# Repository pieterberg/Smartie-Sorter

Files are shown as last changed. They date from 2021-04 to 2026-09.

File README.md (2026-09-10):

# Smartie Sorter 3000

   

Smartie Sorter 3000 project for sorting Smarties and M&M's based on their colour using the TCS3200 colour sensor built into a mini arcade game enclosure.

The project was written using C++ and runs on an Arduino Nano R4 microcontroller. The mini arcade game enclosure was designed using Fusion 360. The physical components were either laser-cut out of MDF and acrylic, or 3D printed using a Bambu Lab X1 Series 3D printer.

## Arduino Sketches

- The [smartie_sorter.ino](smartie_sorter/smartie_sorter.ino) sketch contains the main logic for the Smartie Sorter 3000 mini arcade game. First, the sketch initialises the Smartie Sorter 3000 after the power is switched on. The user interaction is handled by reading the button presses and providing feedback to the user through flashing the built-in LED lights. The RGB spectra of the Smarties and M&M chocolates are measured using the TCS3200 colour sensor and their colours are determined using the trained colour-detection classifier. The chocolates are then sorted using the servo motors by reading the calibrated positions stored in the EEPROM. Finally, the total number of sorted chocolates is updated and stored in the EEPROM.

- [Management.ino](management/management.ino) provides the required utilities to manage the Smartie Sorter 3000. The sketch contains code to initialise the EEPROM addresses of new Arduino boards. The management tool can then be used to generate training datasets of the RGB spectra measured by the TCS3200 colour sensor in order to train the colour-detection classifiers. An interface for calibrating the servo motors is also provided. Finally, an option is available to view the total number of sorted Smarties and M&M chocolates. These utilities can be accessed through a 9600 Baud serial channel.

## Arduino CLI

A Makefile is provided that can be used to compile and upload the Arduino sketches using the [Arduino CLI](https://github.com/arduino/arduino-cli). The make commands should all be run from the project's root directory.

First, run the install command to install the required core for the Arduino Nano R4 board. This will install the Arduino Renesas core (arduino:renesas_uno) if it is not already installed.

```shell
make install
```

The upload command can be used to compile and upload the smartie_sorter.ino sketch to the Arduino Nano R4 board. Replace the `port` parameter with the relevant port of the Arduino Nano R4 board. The ports of the attached Arduino boards can be viewed by running `arduino-cli board list` in the terminal.

```shell
make upload port=COM7
```

The upload-management command can be used to compile and upload the management.ino sketch to the Arduino Nano R4 board. Once again replace the `port` parameter with the relevant port of the Arduino Nano R4 board.

```shell
make upload-management port=COM7
```

## Git Signatures

The [signatures](./signatures) folder contains the required public SSH keys to verify the git commit signatures. These public SSH keys have been configured in the allowed_signers file.

Run the following command in the project's root directory to configure the repository's local git config file to use the allowed_signers file for verifying the git commmit signatures:

```shell
git config --local gpg.ssh.allowedSignersFile "./signatures/allowed_signers"
```

## Documentation

- [Components.md](documentation/components.md) provides information about the components used in the design of the Smartie Sorter 3000's mini arcade game enclosure. First, it provides information about the different types of components used in the design of the Smartie Sorter 3000's mini arcade game enclosure. Thereafter, it provides information about laser cutting the wooden panels and acrylic components. Finally, it provides information about the Fusion 360 computer aided design (CAD) files.

- [Design.md](documentation/design.md) provides information about the design of the Smartie Sorter 3000. First, it provides information about the name sign present at the top of the Smartie Sorter 3000's mini arcade game enclosure. Thereafter, it provides information about the Smartie Sorter 3000's colour scheme. Finally, it provides information about the sorted Smartie and M&M locations.

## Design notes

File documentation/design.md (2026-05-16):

# Design 

This document provides information about the design of the Smartie Sorter 3000. First, Section 1 provides information about the name sign present at the top of the Smartie Sorter 3000's mini arcade game enclosure. Thereafter, Section 2 provides information about the Smartie Sorter 3000's colour scheme. Finally, Section 3 provides information about the sorted Smartie and M&M locations.

The Smartie Sorter 3000 logo, colour scheme, and sorted Smartie and M&M locations were created using Affinity Designer. The `.afdesign` files are available in the [affinity_designer](https://github.com/pieterberg/Smartie-Sorter/tree/main/design/affinity_designer) folder.

### Table of Contents

- [1. Name Sign](#1-name-sign)
  - [1.1. Digital File](#11-digital-file)
  - [1.2. Enclosure Placement](#12-enclosure-placement)
- [2. Colour Scheme](#2-colour-scheme)
  - [2.1. Enclosure Design](#21-enclosure-design)
  - [2.2. Arcade Game Buttons](#22-arcade-game-buttons)
  - [2.3. Smartie Colours](#23-smartie-colours)
  - [2.4. M\&M Colours](#24-mm-colours)
- [3. Sorting Locations](#3-sorting-locations)
  - [3.1. Smartie Locations](#31-smartie-locations)
  - [3.2. M\&M Locations](#32-mm-locations)

## 1. Name Sign

This section provides information about the name sign present at the top of the Smartie Sorter 3000's mini arcade game enclosure.

The "3000" in the Smartie Sorter 3000's name comes from the TCS3200 colour sensor that the Smartie Sorter 3000 uses to determine the Smartie and M&M colours.

The logo was stylized using the Bauhaus 93 typeface.

### 1.1. Digital File

The Smartie Sorter 3000 logo is presented in Figure 1. The logo has 8 slanted stripes that correspond to the 8 Smartie colours, which are presented in Section 2.3. 

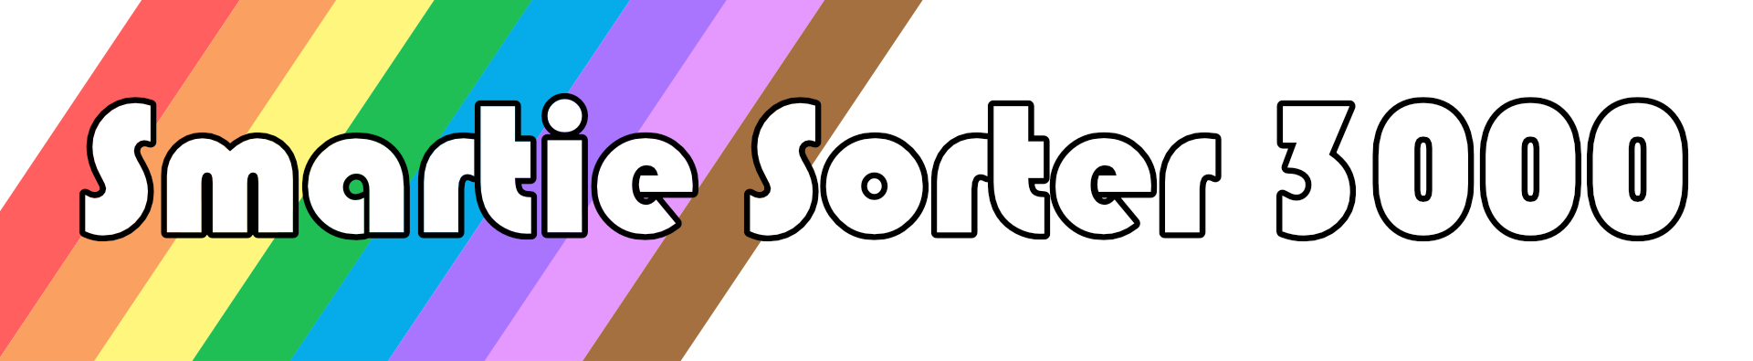
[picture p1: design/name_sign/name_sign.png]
Name sign


Figure 1: The Smartie Sorter 3000 logo used for the name at the top of the mini arcade game enclosure

The [name sign](https://github.com/pieterberg/Smartie-Sorter/tree/main/design/name_sign) folder contains both a `.png` version and an `.svg` version of the Smartie Sorter 3000 logo.

### 1.2. Enclosure Placement

The Smartie Sorter 3000 logo was printed on a 270 mm x 55 mm vinyl sticker and affixed to the Name Sign component.

The Name Sign component is backlit using 12 V LED strips present in the top-section of the mini arcade game enclosure, as documented in [electronics.md](https://github.com/pieterberg/Smartie-Sorter/blob/main/documentation/electronics.md).

## 2. Colour Scheme

This section presents the colour schemes used to design the Smartie Sorter 3000. The colour schemes and hex codes of the mini arcade game enclosure, arcade game buttons, Smartie chocolates, and M&M chocolates are provided.

The [colour_scheme](https://github.com/pieterberg/Smartie-Sorter/tree/main/design/colour_scheme) folder contains .png versions of the colour schemes.

### 2.1. Enclosure Design

The colour scheme used for the design of the mini arcade game enclosure is presented by Figure 2. The outside surfaces of the mini arcade game enclosure are painted brown while the internal surfaces of the mini arcade game enclosure are painted white.

The brown colour used for the design of the mini arcade game enclosure is based on the colour of the Rust-Oleum Painter's Touch Ultra Cover satin Nutmeg paint.

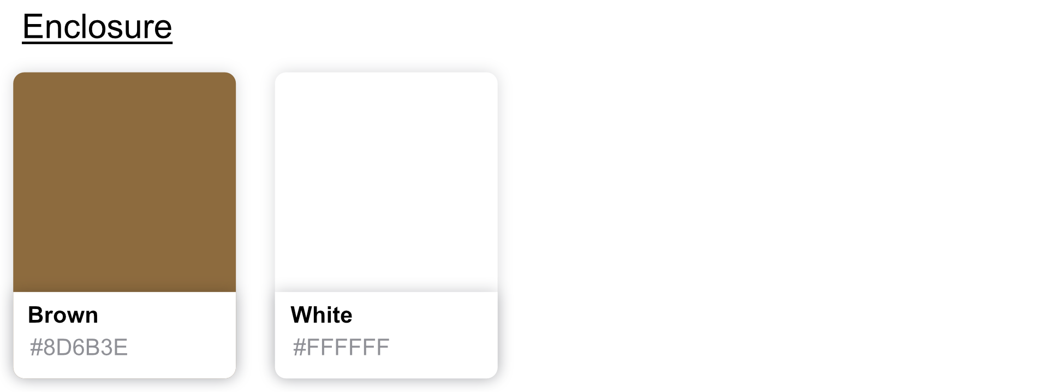
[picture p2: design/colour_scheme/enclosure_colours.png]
Enclosure colour scheme


Figure 2: The mini arcade game enclosure's colour scheme

The hex codes for the mini arcade game enclosure's colour scheme are provided in Table 1.

Table 1: The hex codes for the mini arcade game enclosure's colour scheme

| Enclosure Colours |  Hex code |
|---|:---:|
| Brown | `#8D6B3E` |
| White | `#FFFFFF` |

### 2.2. Arcade Game Buttons

The Smartie Sorter 3000 uses three Sanwa arcade game buttons to control the sorting process: one light-blue arcade game button and two white arcade game buttons. Figure 3 presents the colour scheme for the selected Sanwa arcade game buttons.

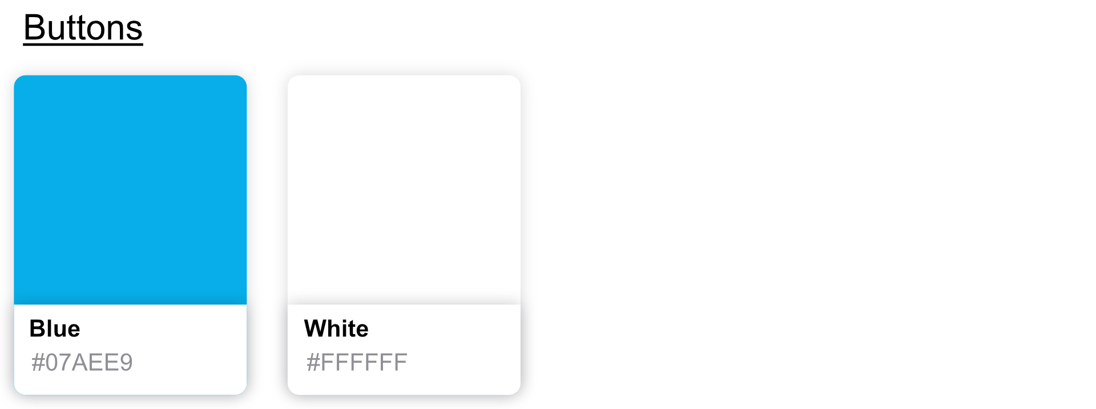
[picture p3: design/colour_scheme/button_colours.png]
Button colour scheme


Figure 3: The Sanwa arcade game buttons' colour scheme

The hex codes for the Sanwa arcade game buttons' colour scheme are provided in Table 2.

Table 2: The hex codes for the Sanwa arcade game buttons' colour scheme

| Arcade Button Colours |  Hex code |
|---|:---:|
| Blue | `#07AEE9` |
| White | `#FFFFFF` |

Information about the arcade game buttons and how they control the sorting process is provided in [sorting.md](https://github.com/pieterberg/Smartie-Sorter/blob/main/documentation/sorting.md).

### 2.3. Smartie Colours

There are 8 different Smartie colours, namely: red, orange, yellow, green, blue, mauve, pink, and brown. Figure 4 presents the Smarties colour scheme.

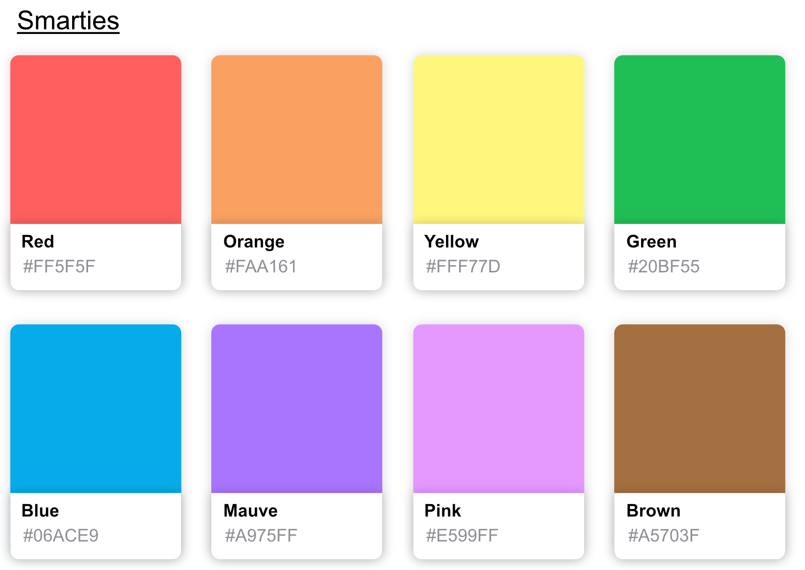
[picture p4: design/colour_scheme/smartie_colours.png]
Smartie colours


Figure 4: The Smarties colour scheme

The hex codes for the Smarties colour scheme are provided in Table 3.

Table 3: The hex codes for the Smarties colour scheme

| Smartie Colours |  Hex code |
|---|:---:|
| Red | `#FF5F5F` |
| Orange | `#FAA161` |
| Yellow | `#FFF77D` |
| Green | `#20BF55` |
| Blue | `#06ACE9` |
| Mauve | `#A975FF` |
| Pink | `#E599FF` |
| Brown | `#A5703F` |

### 2.4. M&M Colours

There are 6 different M&M colours, namely: red, orange, yellow, green, blue, and brown. Figure 5 presents the official M&M colour scheme.

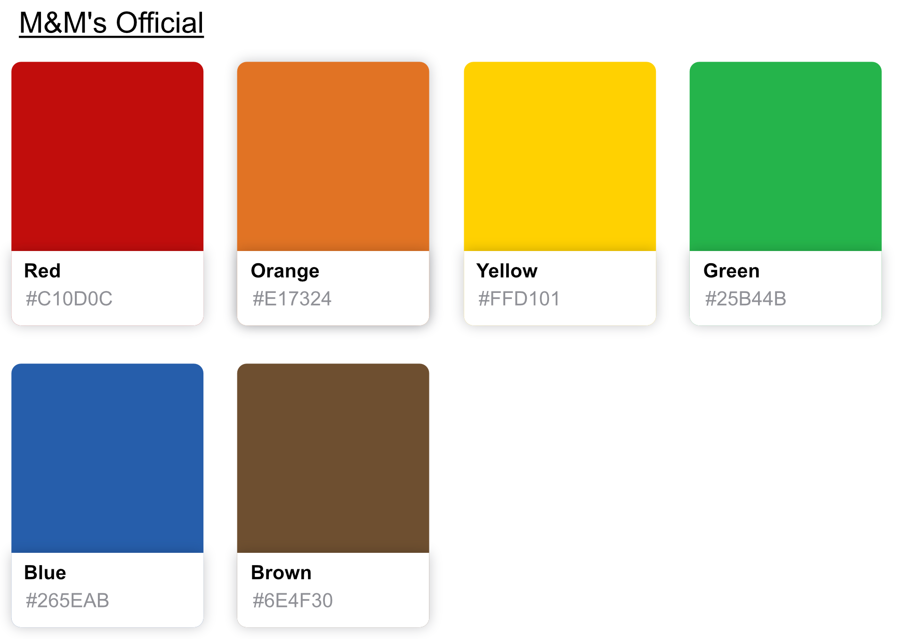
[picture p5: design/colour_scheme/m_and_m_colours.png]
M&M colours


Figure 5: The official M&M colour scheme

The hex codes for the official M&M colour scheme are provided in Table 4.

Table 4: The hex codes for the official M&M colour scheme

| Official M&M Colours |  Hex code |
|---|:---:|
| Red | `#C10D0C` |
| Orange | `#E17324` |
| Yellow | `#FFD101` |
| Green | `#25B44B` |
| Blue | `#265EAB` |
| Brown | `#6E4F30` |

## 3. Sorting Locations

Once sorted, the Smarties and M&M's are transferred to the acrylic Sorted Smarties Collector component. The Sorted Smarties Collector component contains 8 compartments, and the locations of the sorted Smarties and M&M's are dependent on the value of the `SORTING_MODE` property. 

The Smartie Sorter 3000 can operate in 2 different sorting modes, as shown by Table 5.

Table 5: Sorting modes and their descriptions

| Sorting Mode | Description |
|---|---|
| Uncollated | Smarties and M&M's of the same colour are grouped together in the same compartment.  |
| Collated | Consecutive Smarties and M&Ms of the same colour end up in consecutive compartments. |

Information about setting and viewing the value of the `SORTING_MODE` property is provided in [sorting.md](sorting.md).

### 3.1. Smartie Locations

Figure 6 provides the sorted Smartie locations. The uncollated Smarties locations correspond with the Smartie colour scheme that was presented in Figure 4.

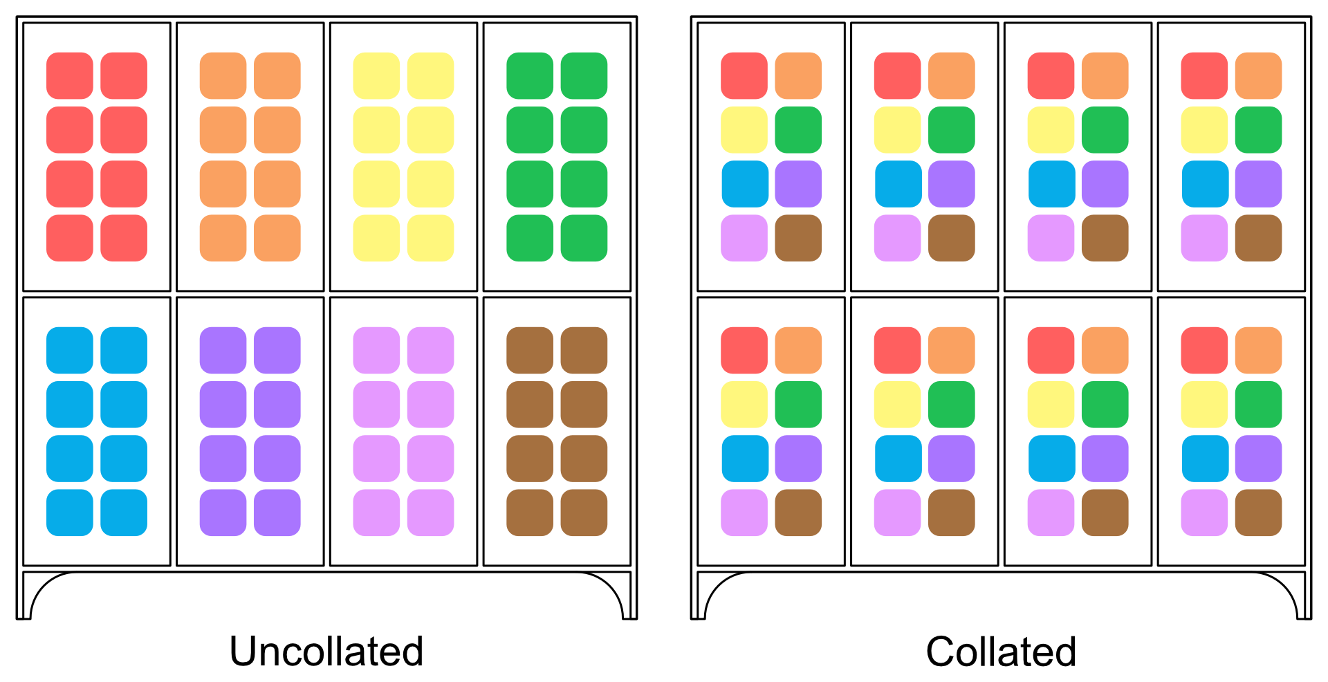
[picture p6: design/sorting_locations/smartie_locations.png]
Smartie Locations


Figure 6: The uncollated and collated sorted Smartie locations

### 3.2. M&M Locations

Figure 6 provides the sorted M&M locations. The uncollated M&M locations correspond with the official M&M colour scheme that was presented in Figure 5. Since there are only 6 M&M colours, only the first 6 compartments of the Sorted Smarties Collector component are used.

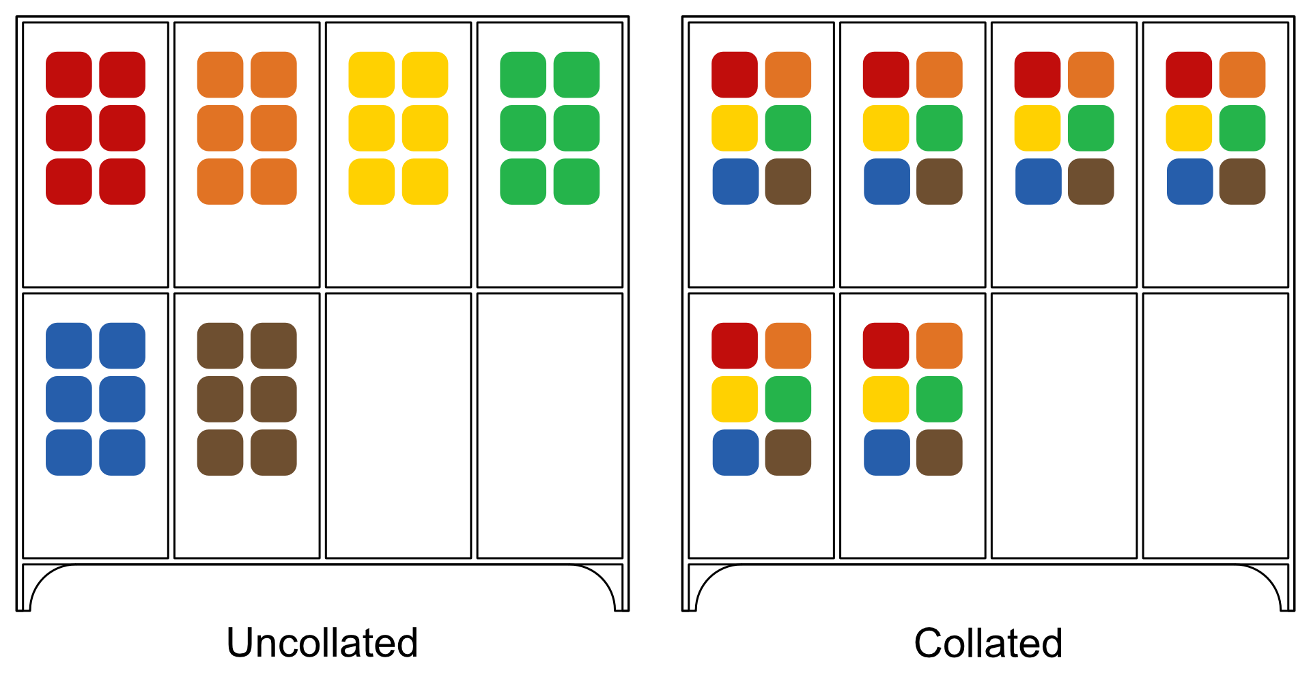
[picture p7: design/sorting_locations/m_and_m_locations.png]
M&M Locations


Figure 7: The uncollated and collated sorted M&M locations

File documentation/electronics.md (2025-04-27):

# Electronics

The electronic aspects of the Smartie Sorter 3000 are presented in this document. First, Section 1 lists the electronic components used for the mini arcade game enclosure. Then, Section 2 provides the breadboard and circuit schematics of the mini arcade game enclosure.

All circuit schematics were designed using Fritzing. The Fritzing file is available in the [Fritzing](https://github.com/pieterberg/Smartie-Sorter/tree/main/assets/electronics/fritzing) folder.

### Table of Contents

- [1. Component list](#1-component-list)
- [2. Schematics](#2-schematics)
  - [2.1. Breadboard Schematic](#21-breadboard-schematic)
  - [2.2. Circuit Schematic](#22-circuit-schematic)

## 1. Component list

The Smartie Sorter 3000 uses an Arduino Nano microcontroller. Table 1 lists the electronic components used for the mini arcade game enclosure.

The Smartie Sorter 3000 has two different circuits, namely a 9V circuit used to power the Arduino Nano and circuit components, and a 12V circuit used to power the LED strips. The 12V LED strips are controlled by the Arduino Nano using a 2N2222 NPN transistor.

Table 1: Electronic component list

| Component | Amount |
|---|:---:|
| Arduino Nano | 1x |
| 9V batteries | 2x |
| 1.5V batteries | 2x |
| 9V battery holders | 2x |
| 3V battery holder | 1x |
| Light blue Sanwa arcade game button | 1x |
| White Sanwa arcade game buttons | 2x |
| Pull-up resistors | 3x |
| 2N2222 transistor | 1x |
| Transistor resistor | 1x |
| 4-part 12V LED strips | 2x |
| 5-part 12V LED strips | 4x |
| Power switch | 1x |

## 2. Schematics

The circuit schematics were designed using Fritzing, and are presented in this section.

### 2.1. Breadboard Schematic

The breadboard schematic of the Smartie Sorter 3000 is presented in Figure 1. In Figure 1, the left breadboard represents the 12V circuit while the right breadboard represents the 9V circuit. The grounds of the two breadboards are connected for the 2N2222 NPN transistor to work. The [electronics](https://github.com/pieterberg/Smartie-Sorter/tree/main/assets/electronics) folder contains both a .png and an .svg version of the breadboard schematic.

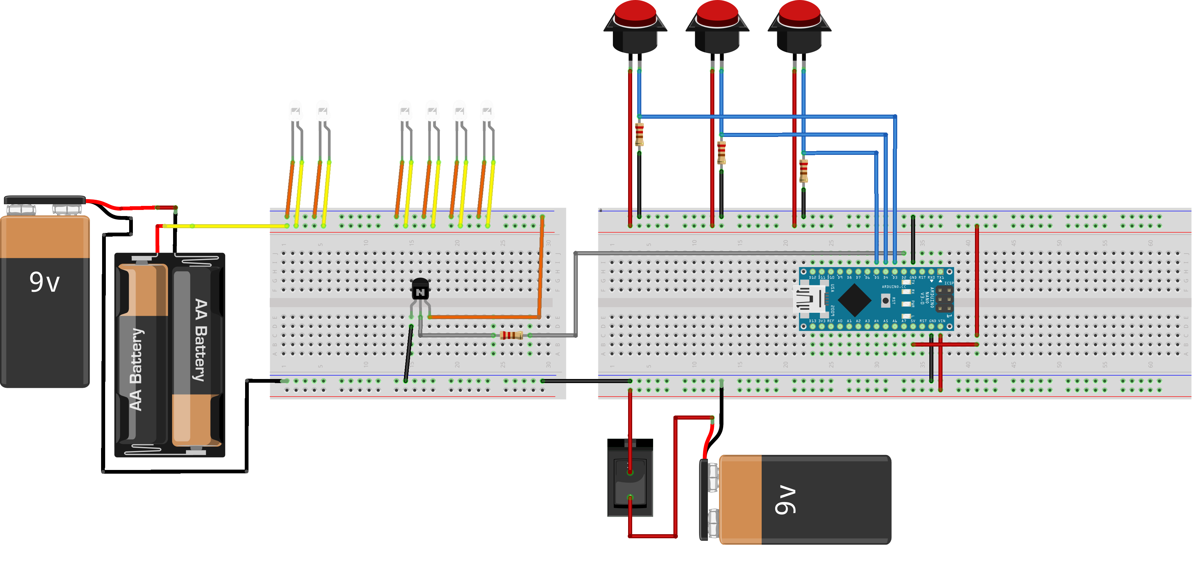
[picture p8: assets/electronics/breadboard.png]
Breadboard schematic


Figure 1: Breadboard schematic of the Smartie Sorter 3000. The left breadboard represents the 12V circuit while the right breadboard represents the 9V circuit.

### 2.2. Circuit Schematic

The circuit schematic of the Smartie Sorter 3000 is presented in Figure 2. In Figure 2, the left loop represents the 12V circuit while the right loop represents the 9V circuit. The grounds of the two loops are connected for the 2N2222 NPN transistor to work. The [electronics](https://github.com/pieterberg/Smartie-Sorter/tree/main/assets/electronics) folder contains both a .png and an .svg version of the circuit schematic.

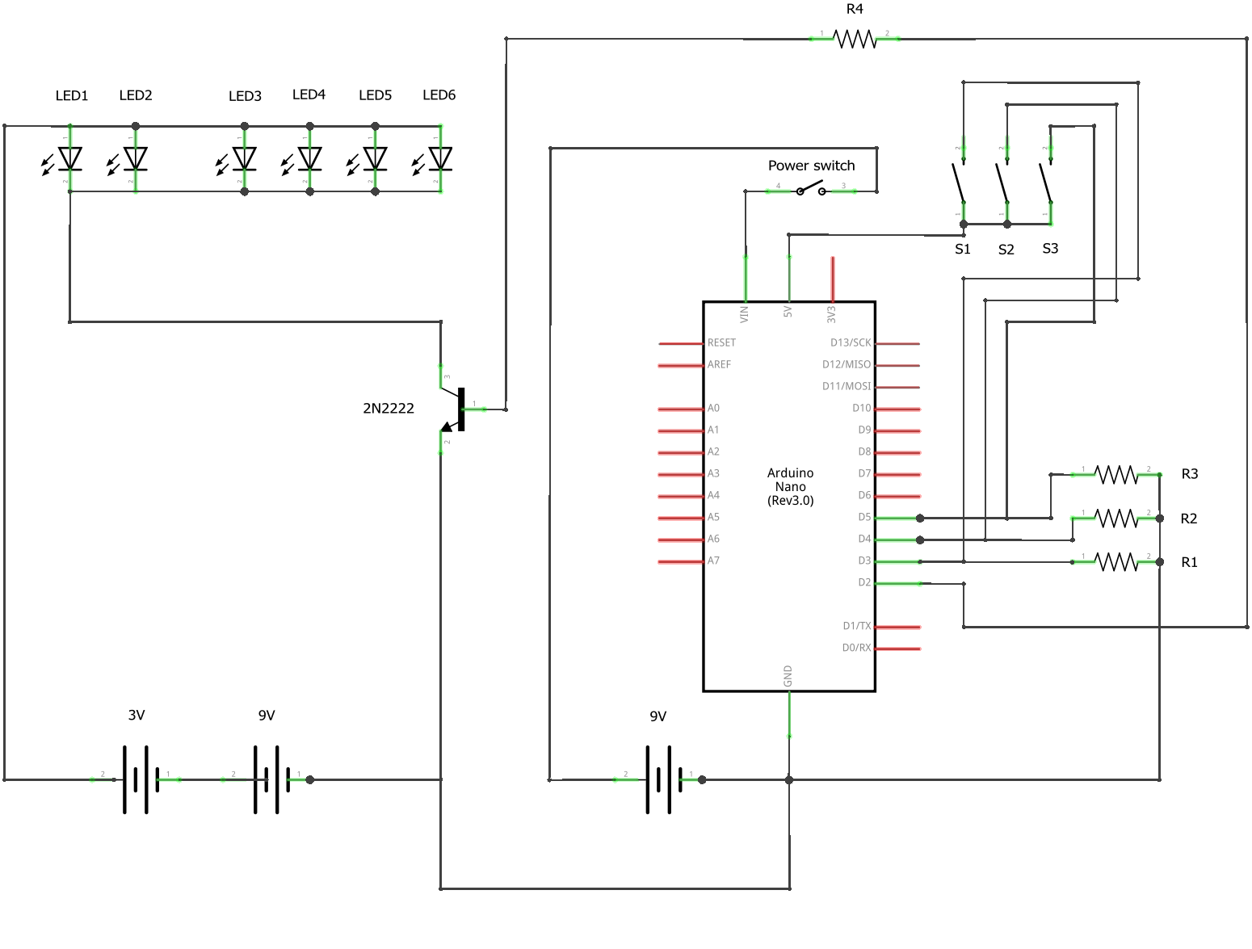
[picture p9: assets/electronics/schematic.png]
Schematic


Figure 2: Circuit schematic of the Smartie Sorter 3000. The left loop represents the 12V circuit while the right loop represents the 9V circuit.

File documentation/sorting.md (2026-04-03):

# Sorting

### Table of Contents

- [1. Sorting Procedure](#1-sorting-procedure)
- [2. Operating Modes](#2-operating-modes)
  - [2.1. Enumerated Values](#21-enumerated-values)
  - [2.2. Default Values](#22-default-values)
- [3. Control](#3-control)
  - [3.1. Buttons](#31-buttons)
  - [3.2. Combinations Mode](#32-combinations-mode)
  - [3.3. Combinations](#33-combinations)

## 1. Sorting Procedure

## 2. Operating Modes

There are three different operating properties that control the sorting behaviour of the Smartie Sorter 3000, namely:

- `SORTING_STATE`
- `CHOCOLATE_MODE`
- `SORTING_MODE`

Each of these properties have two different possible values that they can have at any given time. Section 2.1 provides more information about the different values that the operating properties can have while Section 2.2 provides the default values for each operating property.

### 2.1. Enumerated Values

The values of the three operating properties are tracked using enums. The Smartie Sorter 3000 must have a value for each property at any given time.

The `SORTING_STATE` property controls whether the Smartie Sorter 3000 is currently performing the sorting procedure that was outlined in Section 1. The two possible enumerated values are:

- SORTING
- NOT_SORTING

The `CHOCOLATE_MODE` property allows the Smartie Sorter 3000 to switch between sorting Smarties and sorting M&M's. The two possible enumerated values are:

- SMARTIES
- M_AND_M_S

The `SORTING_MODE` property allows the Smartie Sorter 3000 to switch between grouping the same-coloured Smarties and M&M's together (uncollated) and grouping the Smarties and M&M's in such a way that consecutive chocolates of the same colour end up in consecutive compartments (collated). The two possible enumerated values are:

- UNCOLLATED 
- COLLATED

More information about the sorting locations is provided in [design.md](design.md).

### 2.2. Default Values

The default values of the three operating properties are given by Table 1. These values have been hard-coded into the Arduino sketch and represent the values that the operating properties will have when powering on the Smartie Sorter 3000 for the first time.

Table 1: The default values of the operating properties

| Property | Default Value |
|---|---|
| `SORTING_STATE`  | NOT_SORTING |
| `CHOCOLATE_MODE` | SMARTIES |
| `SORTING_MODE` | UNCOLLATED |

Subsequent changes made to the `CHOCOLATE_MODE` property and the `SORTING_MODE` property will be stored in the EEPROM. However, the `SORTING_STATE` property will always be set to NOT_SORTING when powering on the Smartie Sorter 3000.

## 3. Control

Control of the Smartie Sorter 3000 is achieved through the use of arcade game buttons to set the values of the three operating properties that were defined in Section 2.

### 3.1. Buttons

The Smartie Sorter 3000 uses three Sanwa arcade game buttons to control the sorting process. As mentioned in [design.md](https://github.com/pieterberg/Smartie-Sorter/blob/main/documentation/design.md), the arcade game buttons consist of one light-blue arcade game button and two white arcade game buttons. Table 2 provides the normal behaviour of the arcade game buttons.

Table 2: The normal behaviour of the arcade game buttons

| Mode Number | Button | Symbol | Action |
|:---:|---|:---:|---|
| 3 | Blue arcade game button | `B` | Enters the "combination" mode for setting the values of the `CHOCOLATE_MODE` and `SORTING_MODE` properties. |
| 1 | Left white arcade game button  | `L` | Starts the sorting procedure by setting the value of the `SORTING_STATE` property to SORTING. |
| 2 | Right white arcade game button | `R` | Stops the sorting procedure by setting the value of the `SORTING_STATE` property to NOT_SORTING. |

The Arduino sketch continuously monitors for button presses during the sorting procedure, and the built-in LEDs will flash a certain number of times, corresponding to the mode number, when the `SORTING_STATE` property changes.

### 3.2. Combinations Mode

The "combinations" mode can be used to set the values of the `CHOCOLATE_MODE` and `SORTING_MODE` properties through entering a combination of left and right white arcade game button presses. 

The procedure to enter a combination is as follows:

1. Press the blue arcade game button to enter the "combinations" mode
2. Enter a combination of left and right white arcade game button presses
3. Press the blue arcade game button again to exit the "combinations" mode

The Smartie Sorter 3000 will enter the selected operating mode if a valid combination of white arcade game button presses was entered. The built-in LEDs will flash a certain number of times, corresponding to the mode number, to confirm that the combination has been accepted.

### 3.3. Combinations

A numeric system is used to keep track of the white arcade game button presses during "combination" mode. Presses of the left white arcade game button (`L`) count +1 point while presses of the right white arcade game button (`R`) count +10 points. The selected operating mode is then entered based on the total points score. Table 3 provides the supported combinations and their respective actions.

Table 3: The combinations for setting the values of the `CHOCOLATE_MODE` and `SORTING_MODE` properties

| Mode Number | Combination | Numeric Value | Action |
|:---:|---|:---:|---|
| - | `L` | 1 | Displays the active chocolate mode. |
| - | `R` | 10 | Displays the active sorting mode. |
| 4 | `L L R L L R L` | 25 | Sets the value of `CHOCOLATE_MODE` to SMARTIES.  |
| 5 | `L R L L R L R` | 34 | Sets the value of `CHOCOLATE_MODE` to M_AND_M_S. |
| 6 | `R L R R R L R` | 52 | Sets the value of `SORTING_MODE` to UNCOLLATED.  |
| 7 | `R R L R L L R` | 43 | Sets the value of `SORTING_MODE` to COLLATED. |

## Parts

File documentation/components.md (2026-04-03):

# Components

This documents provides information about the components used in the design of the Smartie Sorter 3000's mini arcade game enclosure. First, Section 1 provides information about the different types of components used in the design of the Smartie Sorter 3000's mini arcade game enclosure. Thereafter, Section 2 provides information about laser cutting the wooden panels and acrylic components. Finally, Section 3 provides information about the Fusion 360 computer aided design (CAD) files.

### Table of Contents

- [1. Components](#1-components)
  - [1.1. Wooden Components](#11-wooden-components)
  - [1.2. Acrylic Components](#12-acrylic-components)
  - [1.3. 3D Printed Components](#13-3d-printed-components)
  - [1.4. Labels](#14-labels)
- [2. Laser Cutting](#2-laser-cutting)
  - [2.1. DXF Files Folder Structure](#21-dxf-files-folder-structure)
  - [2.2. Name Sign](#22-name-sign)
  - [2.3. Smartie Slide](#23-smartie-slide)
  - [2.4. Sorted Smarties Collector](#24-sorted-smarties-collector)
  - [2.5. Wooden Panels](#25-wooden-panels)
- [3. Fusion 360 Files](#3-fusion-360-files)
  - [3.1. Resources](#31-resources)
  - [3.2. Fusion 360 Folder Structure](#32-fusion-360-folder-structure)

## 1. Components

There are eight different types of components used in the design of the Smartie Sorter 3000, namely: 

1. 3D printed components
2. Acrylic components
3. Chocolates
4. Connectors
5. Electronics
6. Labels
7. Supports
8. Wooden panels

This section provides information about the wooden components (wooden panels and supports), acrylic components, 3D printed components, and labels.

Information about the electronic components is provided in [electronics.md](https://github.com/pieterberg/Smartie-Sorter/blob/main/documentation/electronics.md).

### 1.1. Wooden Components

The wooden components are comprised of medium density fibreboard (MDF) panels and pine supports.

The wooden panels should be laser cut out of:

- 6 mm MDF

Section 2.5 provides more information about laser cutting the wooden panels.

The pine supports should be cut from:

- 12 mm pine
- 21 mm × 21 mm pine

The wooden components should be painted according to the colour scheme provided in [design.md](https://github.com/pieterberg/Smartie-Sorter/blob/main/documentation/design.md). The wooden components should then be sealed using a clear coat.

### 1.2. Acrylic Components

Clear acrylic is used for the Name Sign, Smartie Slide, and Sorted Smarties Collector.

The Name Sign should be laser cut out of:

- 6 mm clear acrylic

Section 2.2 provides more information about laser cutting the Name Sign.

The Smartie Slide and Sorted Smarties Collector are assemblies whose panels have been designed to fit together using finger joints.

The Smartie Slide panels and Sorted Smarties Collector panels should be laser cut out of:

- 3 mm transparent acrylic

Section 2.3 and 2.4 provide more information about laser cutting the Smartie Slide panels and Sorted Smarties Collector panels, respectively.

The Smartie Slide and Sorted Smarties Collector should then be assembled by welding their respective panels together using an acrylic cement such as ACRIFIX® 1S 0117. The acrylic cement should be applied using a fine needle and syringe, such as a 0.6&nbsp;mm × 32&nbsp;mm needle and a 1&nbsp;mL syringe.

### 1.3. 3D Printed Components

3D printed components are used for the Colour Detection Mechanism and to house the electronic components.

The 3D printed components should be printed using a 3D printer, such as the Bambu Lab X1 Series 3D printer, using:

- White PLA filament

A layer height of 0.16 mm should be used for a high print quality.

An infill setting of 35% should be used to maximise the strength of the 3D printed components while minimizing their weight.

The Smartie Hopper has a 10° slant on its front face which should be used as the bottom face when 3D printing the Smartie Hopper.

The 3D printed components should then be glued in place. The structural 3D printed components, such as the Electronics Holder, should be glued using a clear epoxy adhesive such as the Pattex Clear Power Epoxy. The Servo Horn should also be glued to the Smartie Arm using the clear epoxy adhesive.

The 3D printed components that are involved in the Colour Detection Mechanism should be glued using a cyanoacrylate adhesive such as the Pattex Ultra Gel Super Glue.

### 1.4. Labels

The labels should be printed using a label maker, such as the Brother PT-H110 label maker, using:

- 12 mm black on white laminated tape

The labels should then be affixed in position and sealed using a clear coat.

## 2. Laser Cutting

The outlines of the wooden panels and acrylic components have been exported as DXF files and are available in the [dxf_files](../assets/dxf_files) folder.

These DXF files can be used for laser cutting the wooden panels and acrylic components out of MDF and clear acrylic, respectively.

### 2.1. DXF Files Folder Structure

The folder structure of the dxf_files folder is presented below:

```
.
|__ assets
    |__ dxf_files
        |__ acrylic_components
        |   |__ name_sign
        |   |__ smartie_slide
        |   |__ sorted_smarties_collector
        |__ wooden_panels
```

### 2.2. Name Sign

Laser cut the following DXF file in the [name_sign](../assets/dxf_files/acrylic_components/name_sign) folder out of 6 mm clear acrylic to create the Name Sign:

- 1 × name_sign.dxf

### 2.3. Smartie Slide

Laser cut the following DXF files in the [smartie_slide](../assets/dxf_files/acrylic_components/smartie_slide) folder out of 3 mm clear acrylic to construct the Smartie Slide:

- 1 × back_panel.dxf
- 1 × bottom_panel.dxf
- 1 × front_panel.dxf
- 2 × middle_panel.dxf
- 2 × side_panel.dxf
- 1 × slide_panel.dxf
- 1 × top_panel.dxf

### 2.4. Sorted Smarties Collector

Laser cut the following DXF files in the [sorted_smarties_collector](../assets/dxf_files/acrylic_components/sorted_smarties_collector) folder out of 3 mm clear acrylic to construct the Sorted Smarties Collector:

- 1 × back_panel.dxf
- 3 × divider_bottom.dxf
- 3 × divider_top.dxf
- 1 × front_panel.dxf
- 2 × horizontal_panel.dxf
- 2 × side_panel.dxf
- 1 × top_panel.dxf

### 2.5. Wooden Panels

Laser cut the following DXF files in the [wooden_panels](../assets/dxf_files/wooden_panels) folder out of 6 mm MDF to construct the mini arcade game enclosure:

- 1 × back_panel.dxf
- 1 × base_plate.dxf
- 1 × bottom_access_panel.dxf
- 1 × colour_detection_mechanism_top_panel.dxf
- 1 × control_panel_bottom.dxf
- 1 × control_panel_front.dxf
- 1 × control_panel_top.dxf
- 1 × front_panel.dxf
- 1 × name_sign_bottom_panel.dxf
- 2 × side_panel.dxf
- 1 × sorted_smarties_cover.dxf
- 1 × sorted_smarties_top_panel.dxf
- 1 × top_access_panel.dxf
- 1 × top_panel.dxf
- 1 × unsorted_smarties_back_panel.dxf
- 1 × unsorted_smarties_top_panel.dxf

## 3. Fusion 360 Files

All components, mechanisms, and assemblies were designed and modelled using Fusion 360.

The CAD files have been exported and are available in the [fusion_360](https://github.com/pieterberg/Smartie-Sorter/tree/main/fusion_360) folder.

### 3.1. Resources

The following Fusion 360 files are available in the fusion_360 folder:

- Fusion 360 archive files (.f3d) of the components
- Fusion 360 archive file (.f3z) of the Colour Detection Mechanism
- Fusion 360 archive file (.f3z) of the Smartie Sorter

### 3.2. Fusion 360 Folder Structure

The folder structure of the fusion_360 folder is presented below:

```
.
|__ fusion_360
    |__ assemblies
    |__ components
        |__ 3d_printed_components
        |   |__ colour_sensor_holder
        |   |__ colour_sensor_servo_seat
        |__ acrylic_components
        |   |__ smartie_slide
        |   |__ sorted_smarties_collector
        |__ chocolates
        |   |__ M&Ms
        |   |__ smarties
        |__ connectors
        |__ electronics
        |__ labels      
        |__ supports
        |__ wooden_panels
```
The Smartie Sorter 3000 assembly is available in the fusion_360 folder.

The Colour Detection Mechanism assembly is available in the [assemblies](https://github.com/pieterberg/Smartie-Sorter/tree/main/fusion_360/assemblies) folder.

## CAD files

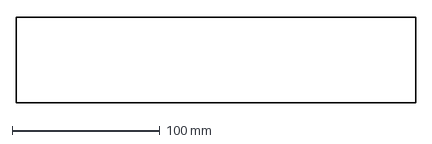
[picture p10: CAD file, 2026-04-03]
assets/dxf_files/acrylic_components/name_sign/name_sign.dxf
270.0 x 57.9 mm

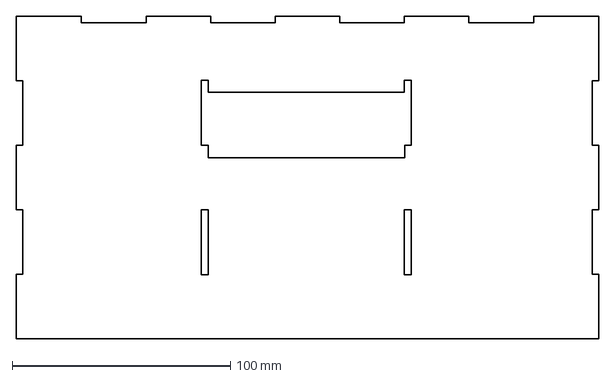
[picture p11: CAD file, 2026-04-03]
assets/dxf_files/acrylic_components/smartie_slide/back_panel.dxf
267.0 x 148.0 mm

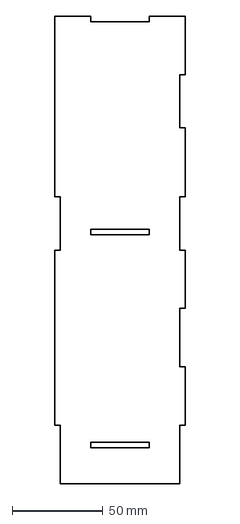
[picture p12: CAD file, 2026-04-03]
assets/dxf_files/acrylic_components/sorted_smarties_collector/side_panel.dxf
72.0 x 258.0 mm

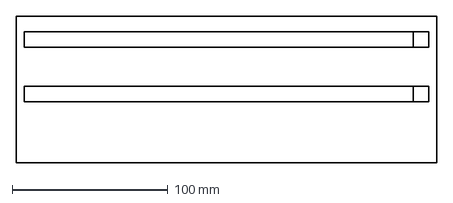
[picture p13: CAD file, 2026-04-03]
assets/dxf_files/wooden_panels/sorted_smarties_top_panel.dxf
270.0 x 94.0 mm

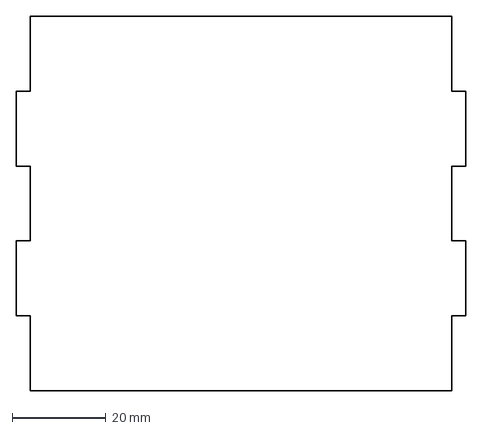
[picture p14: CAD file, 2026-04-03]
assets/dxf_files/acrylic_components/smartie_slide/slide_panel.dxf
96.0 x 80.0 mm

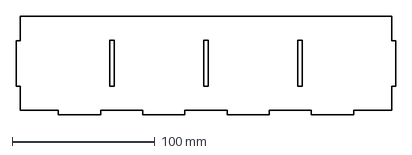
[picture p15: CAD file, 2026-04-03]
assets/dxf_files/acrylic_components/sorted_smarties_collector/horizontal_panel.dxf
266.0 x 69.0 mm

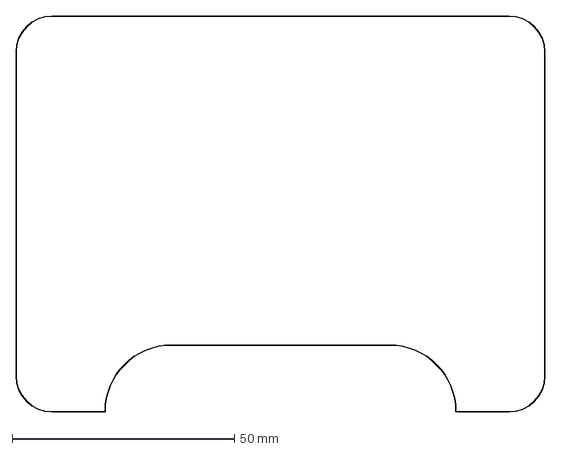
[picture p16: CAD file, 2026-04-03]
assets/dxf_files/wooden_panels/top_access_panel.dxf
119.0 x 89.0 mm

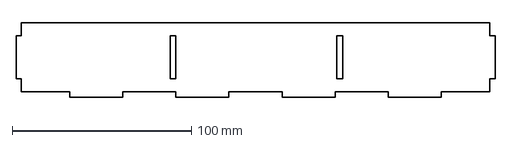
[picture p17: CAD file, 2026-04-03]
assets/dxf_files/acrylic_components/smartie_slide/top_panel.dxf
267.0 x 41.6 mm

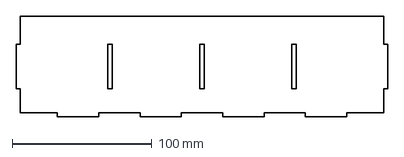
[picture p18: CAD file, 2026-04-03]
assets/dxf_files/acrylic_components/sorted_smarties_collector/top_panel.dxf
266.0 x 72.0 mm

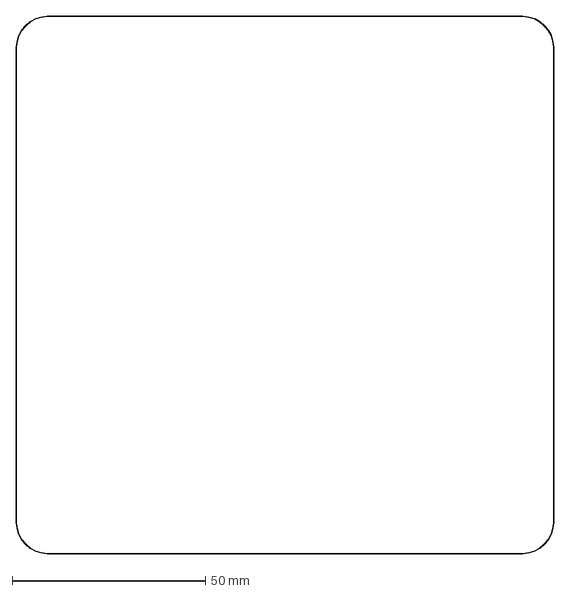
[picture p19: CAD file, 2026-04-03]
assets/dxf_files/wooden_panels/bottom_access_panel.dxf
139.0 x 139.0 mm

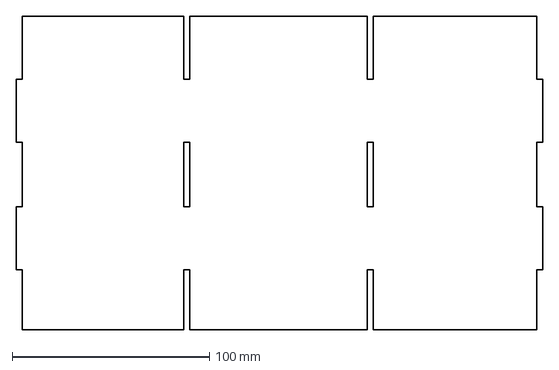
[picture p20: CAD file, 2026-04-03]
assets/dxf_files/acrylic_components/smartie_slide/front_panel.dxf
267.0 x 159.1 mm

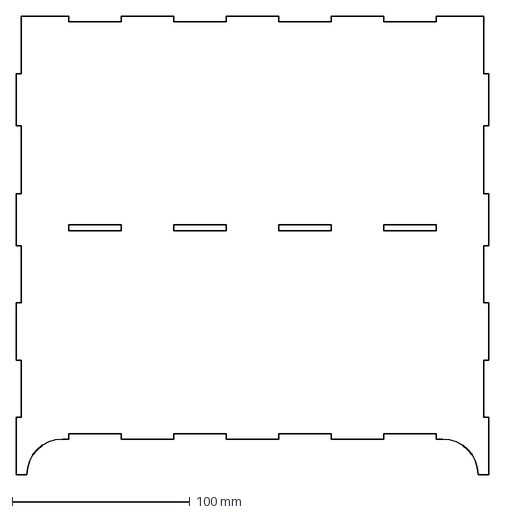
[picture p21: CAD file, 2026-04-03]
assets/dxf_files/acrylic_components/sorted_smarties_collector/back_panel.dxf
266.0 x 258.0 mm

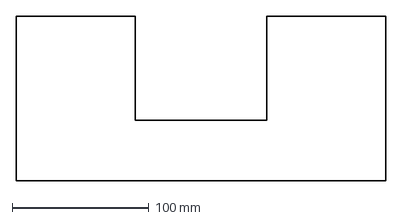
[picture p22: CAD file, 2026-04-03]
assets/dxf_files/wooden_panels/colour_detection_mechanism_top_panel.dxf
270.0 x 120.0 mm

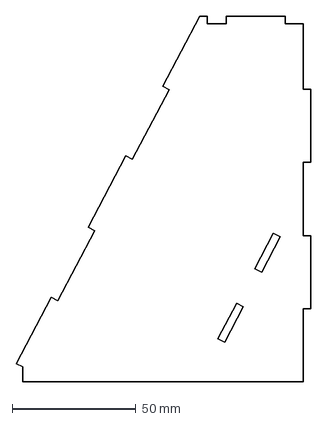
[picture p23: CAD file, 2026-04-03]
assets/dxf_files/acrylic_components/smartie_slide/middle_panel.dxf
119.3 x 148.0 mm

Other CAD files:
assets/dxf_files/acrylic_components/sorted_smarties_collector/divider_bottom.dxf
assets/dxf_files/wooden_panels/unsorted_smarties_top_panel.dxf
assets/dxf_files/acrylic_components/smartie_slide/side_panel.dxf
assets/dxf_files/acrylic_components/sorted_smarties_collector/front_panel.dxf
assets/dxf_files/acrylic_components/smartie_slide/bottom_panel.dxf
assets/dxf_files/acrylic_components/sorted_smarties_collector/divider_top.dxf
assets/dxf_files/wooden_panels/back_panel.dxf
assets/dxf_files/wooden_panels/base_plate.dxf
assets/dxf_files/wooden_panels/control_panel_bottom.dxf
assets/dxf_files/wooden_panels/control_panel_front.dxf
assets/dxf_files/wooden_panels/control_panel_top.dxf
assets/dxf_files/wooden_panels/front_panel.dxf
assets/dxf_files/wooden_panels/name_sign_bottom_panel.dxf
assets/dxf_files/wooden_panels/side_panel.dxf
assets/dxf_files/wooden_panels/sorted_smarties_cover.dxf
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

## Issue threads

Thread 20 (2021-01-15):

Use seperate files

pieterberg, 2021-01-15:
Split the different parts of the programming into different files

- [x] Colour Sensor class
- [x] Seperate file for calibrated values

pieterberg, 2021-02-08:
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 [Code cleanup](https://trello.com/c/gAG9AJBI/13-code-cleanup)

Closed 2021-02-08.

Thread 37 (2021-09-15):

Base Plate

pieterberg, 2021-09-15:

pieterberg, 2021-09-15:
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 [Base Plate](https://trello.com/c/24YgobEo/40-base-plate)

pieterberg, 2021-09-15:
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 [Control Panel Bottom](https://trello.com/c/iMfrKLJ0/41-control-panel-bottom)

pieterberg, 2021-09-15:
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 [Control Panel Bottom](https://trello.com/c/iMfrKLJ0/41-control-panel-bottom)

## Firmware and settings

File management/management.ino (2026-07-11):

// Project name: Smartie Sorter 3000
// Sketch name:  management.ino
// Created by:   Pieter van den Berg
// Created on:   14 July 2025
//
// An Arduino Sketch for managing the Smartie Sorter 3000
//
// Includes the following features:
//
//    - Perform the servo calibration
//    - Perform the colour sensor calibration
//    - View the number of sorted Smarties and M&M's
//    - Initialise the EEPROM
//

#include <EEPROM.h>
#include <math.h>

// Add the EEPROM addresses for the total number of sorted Smarties
const byte eeAddressTotalNumberOfSortedSmartiesRed     = 2;       // unsigned int (2 bytes)
const byte eeAddressTotalNumberOfSortedSmartiesOrange  = 4;       // unsigned int (2 bytes)
const byte eeAddressTotalNumberOfSortedSmartiesYellow  = 6;       // unsigned int (2 bytes)
const byte eeAddressTotalNumberOfSortedSmartiesGreen   = 8;       // unsigned int (2 bytes)
const byte eeAddressTotalNumberOfSortedSmartiesBlue    = 10;      // unsigned int (2 bytes)
const byte eeAddressTotalNumberOfSortedSmartiesMauve   = 12;      // unsigned int (2 bytes)
const byte eeAddressTotalNumberOfSortedSmartiesPink    = 14;      // unsigned int (2 bytes)
const byte eeAddressTotalNumberOfSortedSmartiesBrown   = 16;      // unsigned int (2 bytes)
const byte eeAddressTotalNumberOfSortedSmartiesUnknown = 18;      // unsigned int (2 bytes)

// Add the EEPROM addresses for the total number of sorted M&M's
const byte eeAddressTotalNumberOfSortedMMsRed     = 20;     // unsigned int (2 bytes)
const byte eeAddressTotalNumberOfSortedMMsOrange  = 22;     // unsigned int (2 bytes)
const byte eeAddressTotalNumberOfSortedMMsYellow  = 24;     // unsigned int (2 bytes)
const byte eeAddressTotalNumberOfSortedMMsGreen   = 26;     // unsigned int (2 bytes)
const byte eeAddressTotalNumberOfSortedMMsBlue    = 28;     // unsigned int (2 bytes)
const byte eeAddressTotalNumberOfSortedMMsBrown   = 30;     // unsigned int (2 bytes)
const byte eeAddressTotalNumberOfSortedMMsUnknown = 32;     // unsigned int (2 bytes)

void setup() {

  // Begin a serial channel
  Serial.begin(9600);

  // Wait until the serial channel is established before printing the welcome message
  while (!Serial) {
    delay(1);
  }

  // Print the welcome message
  Serial.println(F("Welcome to the Smartie Sorter 3000's management utility"));
  Serial.println();

  // Print a divider
  printDivider();

}

void loop() {

  // Print the main menu
  printMainMenu();

}

// A function for printing the main menu
void printMainMenu() {

  // Create a variable for keeping track of the selected option
  char current_selection = '0';

  // Print the introduction
  Serial.println(F("Smartie Sorter 3000 main menu"));
  Serial.println(F("Please select an option..."));
  Serial.println();

  // Print the list of options
  Serial.println(F("   1. Servo calibration"));
  Serial.println(F("   2. Colour sensor calibration"));
  Serial.println(F("   3. Sorting data"));
  Serial.println(F("   4. EEPROM settings"));
  Serial.println();

  // Read the selected option
  do {
    current_selection = Serial.read();
  } while ((current_selection != '1') && (current_selection != '2') && (current_selection != '3') && (current_selection != '4'));

  // Print a divider
  printDivider();

  // Call the selected function
  switch (current_selection) {
    case '3':
      printSortingDataMenu();
      break;
    case '4':
      printEEPROMMenu();
      break;      
  }
}

// A function for printing the sorting data menu
void printSortingDataMenu() {

  // Create a variable for keeping track of the selected sorting data option
  char current_selection = '0';

  // Print the introduction
  Serial.println(F("Sorting data menu"));
  Serial.println(F("Please select an option..."));
  Serial.println();

  // Print the list of sorting data options
  Serial.println(F("   1. View the number of sorted Smarties"));
  Serial.println(F("   2. View the number of sorted M&M's"));
  Serial.println(F("   3. Reset the number of sorted Smarties"));
  Serial.println(F("   4. Reset the number of sorted M&M's"));
  Serial.println(F("   5. Return to the main menu"));
  Serial.println();

  // Read the selected sorting data option
  do {
    current_selection = Serial.read();
  } while ((current_selection != '1') && (current_selection != '2') && (current_selection != '3') && (current_selection != '4') && (current_selection != '5'));

  // Print a divider
  printDivider();

  // Call the selected sorting data option
  switch (current_selection) {
    case '1':
      viewSortedSmarties();
      break;
    case '2':
      viewSortedMMs(); 
      break;
    case '3':
      confirmResetNumberOfSortedSmarties();
      break;
    case '4':
      confirmResetNumberOfSortedMMs();
      break;
    case '5':
      break;  
  }
}

// A function for printing the EEPROM settings menu
void printEEPROMMenu() {

  // Create a variable for keeping track of the selected EEPROM setting
  char current_selection = '0';

  // Print the introduction
  Serial.println(F("EEPROM settings menu"));
  Serial.println(F("Please select an option..."));
  Serial.println();

  // Print the list of EEPROM settings
  Serial.println(F("   1. Initialise the EEPROM")); 
  Serial.println(F("   2. Return to the main menu"));
  Serial.println();

  // Read the selected EEPROM setting
  do {
    current_selection = Serial.read();
  } while ((current_selection != '1') && (current_selection != '2'));

  // Print a divider
  printDivider();

  // Call the selected EEPROM setting
  switch (current_selection) {
    case '1':
      confirmInitialiseEEPROM();
      break;
    case '2':
      break;    
  }
}

// A function for viewing the number of sorted Smarties stored in the EEPROM
void viewSortedSmarties() {

  // Create a variable for keeping track of the selected navigational option
  char current_selection = '0';

  // Create variables to store the number of sorted Smarties stored in the EEPROM
  unsigned int totalNumberOfSortedSmartiesRed     = 0;
  unsigned int totalNumberOfSortedSmartiesOrange  = 0;
  unsigned int totalNumberOfSortedSmartiesYellow  = 0;
  unsigned int totalNumberOfSortedSmartiesGreen   = 0;
  unsigned int totalNumberOfSortedSmartiesBlue    = 0;
  unsigned int totalNumberOfSortedSmartiesMauve   = 0;
  unsigned int totalNumberOfSortedSmartiesPink    = 0;
  unsigned int totalNumberOfSortedSmartiesBrown   = 0;
  unsigned int totalNumberOfSortedSmartiesUnknown = 0;

  // Print the introduction
  Serial.println(F("Now displaying the number of sorted Smarties stored in the EEPROM:"));
  Serial.println();

  // Print the number of sorted Smarties stored in the EEPROM
  Serial.print(F("   Red:     ")); Serial.println(EEPROM.get(eeAddressTotalNumberOfSortedSmartiesRed, totalNumberOfSortedSmartiesRed));
  Serial.print(F("   Orange:  ")); Serial.println(EEPROM.get(eeAddressTotalNumberOfSortedSmartiesOrange, totalNumberOfSortedSmartiesOrange));
  Serial.print(F("   Yellow:  ")); Serial.println(EEPROM.get(eeAddressTotalNumberOfSortedSmartiesYellow, totalNumberOfSortedSmartiesYellow));
  Serial.print(F("   Green:   ")); Serial.println(EEPROM.get(eeAddressTotalNumberOfSortedSmartiesGreen, totalNumberOfSortedSmartiesGreen));
  Serial.print(F("   Blue:    ")); Serial.println(EEPROM.get(eeAddressTotalNumberOfSortedSmartiesBlue, totalNumberOfSortedSmartiesBlue));
  Serial.print(F("   Mauve:   ")); Serial.println(EEPROM.get(eeAddressTotalNumberOfSortedSmartiesMauve, totalNumberOfSortedSmartiesMauve));
  Serial.print(F("   Pink:    ")); Serial.println(EEPROM.get(eeAddressTotalNumberOfSortedSmartiesPink, totalNumberOfSortedSmartiesPink));
  Serial.print(F("   Brown:   ")); Serial.println(EEPROM.get(eeAddressTotalNumberOfSortedSmartiesBrown, totalNumberOfSortedSmartiesBrown));
  Serial.print(F("   Unknown: ")); Serial.println(EEPROM.get(eeAddressTotalNumberOfSortedSmartiesUnknown, totalNumberOfSortedSmartiesUnknown));
  Serial.println();

  Serial.println(F("Please select an option..."));
  Serial.println();

  // Print the list of navigational options
  Serial.println(F("   1. Return to the sorting data menu"));
  Serial.println(F("   2. Return to the main menu"));
  Serial.println();

  // Read the selected navigational option
  do {
    current_selection = Serial.read();
  } while ((current_selection != '1') && (current_selection != '2'));

  // Print a divider
  printDivider();

  // Call the selected navigational function
  switch (current_selection) {
    case '1':
      printSortingDataMenu();
      break;
    case '2':
      break;   
  }
}

// A function for viewing the number of sorted M&Ms stored in the EEPROM
void viewSortedMMs() {

  // Create a variable for keeping track of the selected EEPROM option
  char current_selection = '0';

  // Create variables to store the number of sorted M&M's stored in the EEPROM
  unsigned int totalNumberOfSortedMMsRed     = 0;
  unsigned int totalNumberOfSortedMMsOrange  = 0;
  unsigned int totalNumberOfSortedMMsYellow  = 0;
  unsigned int totalNumberOfSortedMMsGreen   = 0;
  unsigned int totalNumberOfSortedMMsBlue    = 0;
  unsigned int totalNumberOfSortedMMsBrown   = 0;
  unsigned int totalNumberOfSortedMMsUnknown = 0;

  // Print the introduction
  Serial.println(F("Now displaying the number of sorted M&M's stored in the EEPROM:"));
  Serial.println();

  // Print the number of sorted M&M's stored in the EEPROM
  Serial.print(F("   Red:     ")); Serial.println(EEPROM.get(eeAddressTotalNumberOfSortedMMsRed, totalNumberOfSortedMMsRed));
  Serial.print(F("   Orange:  ")); Serial.println(EEPROM.get(eeAddressTotalNumberOfSortedMMsOrange, totalNumberOfSortedMMsOrange));
  Serial.print(F("   Yellow:  ")); Serial.println(EEPROM.get(eeAddressTotalNumberOfSortedMMsYellow, totalNumberOfSortedMMsYellow));
  Serial.print(F("   Green:   ")); Serial.println(EEPROM.get(eeAddressTotalNumberOfSortedMMsGreen, totalNumberOfSortedMMsGreen));
  Serial.print(F("   Blue:    ")); Serial.println(EEPROM.get(eeAddressTotalNumberOfSortedMMsBlue, totalNumberOfSortedMMsBlue));
  Serial.print(F("   Brown:   ")); Serial.println(EEPROM.get(eeAddressTotalNumberOfSortedMMsBrown, totalNumberOfSortedMMsBrown));
  Serial.print(F("   Unknown: ")); Serial.println(EEPROM.get(eeAddressTotalNumberOfSortedMMsUnknown, totalNumberOfSortedMMsUnknown));
  Serial.println();

  Serial.println(F("Please select an option..."));
  Serial.println();

  // Print the list of navigational options
  Serial.println(F("   1. Return to the sorting data menu"));
  Serial.println(F("   2. Return to the main menu"));
  Serial.println();

  // Read the selected navigational option
  do {
    current_selection = Serial.read();
  } while ((current_selection != '1') && (current_selection != '2'));

  // Print a divider
  printDivider();

  // Call the selected navigational function
  switch (current_selection) {
    case '1':
      printSortingDataMenu();
      break;
    case '2':
      break;   
  }
}

// A function asking for confirmation before initialising the EEPROM of new Arduino boads
void confirmInitialiseEEPROM() {

  // Create a variable for keeping track of the selected confirmation option
  char current_selection = '0';

  // Print the introduction
  Serial.println(F("You are about to initialise all of the EEPROM values to zero"));
  Serial.println();
  Serial.println(F("This will reset the:"));
  Serial.println();
  Serial.println(F("   - Operating modes"));
  Serial.println(F("   - Number of sorted Smarties"));
  Serial.println(F("   - Number of sorted M&M's"));
  Serial.println();
  Serial.println(F("Please confirm..."));
  Serial.println();

  // Print the list of confirmation options
  Serial.println(F("   1. Yes"));
  Serial.println(F("   2. No"));
  Serial.println();

  // Read the selected confirmation option
  do {
    current_selection = Serial.read();
  } while ((current_selection != '1') && (current_selection != '2'));

  // Take the selected action
  switch (current_selection) {
    case '1':
      // Initialise the EEPROM
      initialiseEEPROM();
      break;
    case '2':
      // Abort the initialisation process
      Serial.println(F("Initialisation aborted"));
      Serial.println();
      break;   
  }

  Serial.println(F("Please select an option..."));
  Serial.println();

  // Print the list of navigational options
  Serial.println(F("   1. Return to the EEPROM settings menu"));
  Serial.println(F("   2. Return to the main menu"));
  Serial.println();

  // Read the selected navigational option
  do {
    current_selection = Serial.read();
  } while ((current_selection != '1') && (current_selection != '2'));

  // Print a divider
  printDivider();

  // Call the selected navigational function
  switch (current_selection) {
    case '1':
      printEEPROMMenu();
      break;
    case '2':
      break;   
  }
}

// A function for initialising the EEPROM of new Arduino boads
void initialiseEEPROM() {

  Serial.println(F("Initialising the EEPROM..."));
  Serial.println();

  // Initialise the EEPROM
  for (int i = 0; i < EEPROM.length(); i++) {
    EEPROM.write(i,0);

    // Print the progress
    if ( i == round(EEPROM.length() / 10 * 1)) {
      Serial.println(F("   10%"));
    } else if (i == round(EEPROM.length() / 10 * 2)) {
      Serial.println(F("   20%"));
    } else if (i == round(EEPROM.length() / 10 * 3)) {
      Serial.println(F("   30%"));
    } else if (i == round(EEPROM.length() / 10 * 4)) {
      Serial.println(F("   40%"));
    } else if (i == round(EEPROM.length() / 10 * 5)) {
      Serial.println(F("   50%"));
    } else if (i == round(EEPROM.length() / 10 * 6)) {
      Serial.println(F("   60%"));
    } else if (i == round(EEPROM.length() / 10 * 7)) {
      Serial.println(F("   70%"));
    } else if (i == round(EEPROM.length() / 10 * 8)) {
      Serial.println(F("   80%"));
    } else if (i == round(EEPROM.length() / 10 * 9)) {
      Serial.println(F("   90%"));
    }
  }
  Serial.println(F("   100%"));
  Serial.println();

  // Print the completion message
  Serial.println(F("Initialisation complete"));
  Serial.println();
}


// A function asking for confirmation before resetting the number of sorted Smarties stored in the EEPROM
void confirmResetNumberOfSortedSmarties() {

  // Create a variable for keeping track of the selected confirmation option
  char current_selection = '0';

  // Print the introduction
  Serial.println(F("You are about to reset the number of sorted Smarties:"));
  Serial.println(F("Please confirm..."));
  Serial.println();

  // Print the list of confirmation options
  Serial.println(F("   1. Yes"));
  Serial.println(F("   2. No"));
  Serial.println();

  // Read the selected confirmation option
  do {
    current_selection = Serial.read();
  } while ((current_selection != '1') && (current_selection != '2'));

  // Take the selected action
  switch (current_selection) {
    case '1':
      // Reset the number of sorted Smarties
      resetNumberOfSortedSmarties();
      break;
    case '2':
      // Abort the reset process
      Serial.println(F("Reset aborted"));
      Serial.println();
      break;   
  }

  Serial.println(F("Please select an option..."));
  Serial.println();

  // Print the list of navigational options
  Serial.println(F("   1. Return to the sorting data menu"));
  Serial.println(F("   2. Return to the main menu"));
  Serial.println();

  // Read the selected navigational option
  do {
    current_selection = Serial.read();
  } while ((current_selection != '1') && (current_selection != '2'));

  // Print a divider
  printDivider();

  // Call the selected navigational function
  switch (current_selection) {
    case '1':
      printSortingDataMenu();
      break;
    case '2':
      break;   
  }
}

// A function for resetting the number of sorted Smarties stored in the EEPROM
void resetNumberOfSortedSmarties() {

  // Reset the number of sorted Smarties stored in the EEPROM
  EEPROM.put(eeAddressTotalNumberOfSortedSmartiesRed, 0);
  EEPROM.put(eeAddressTotalNumberOfSortedSmartiesOrange, 0);
  EEPROM.put(eeAddressTotalNumberOfSortedSmartiesYellow, 0);
  EEPROM.put(eeAddressTotalNumberOfSortedSmartiesGreen, 0);
  EEPROM.put(eeAddressTotalNumberOfSortedSmartiesBlue, 0);
  EEPROM.put(eeAddressTotalNumberOfSortedSmartiesMauve, 0);
  EEPROM.put(eeAddressTotalNumberOfSortedSmartiesPink, 0);
  EEPROM.put(eeAddressTotalNumberOfSortedSmartiesBrown, 0);
  EEPROM.put(eeAddressTotalNumberOfSortedSmartiesUnknown, 0);

  // Print the completion message
  Serial.println(F("Reset complete"));
  Serial.println();
}

// A function asking for confirmation before resetting the number of sorted M&M's stored in the EEPROM
void confirmResetNumberOfSortedMMs() {

  // Create a variable for keeping track of the selected confirmation option
  char current_selection = '0';

  // Print the introduction
  Serial.println(F("You are about to reset the number of sorted M&M's:"));
  Serial.println(F("Please confirm..."));
  Serial.println();

  // Print the list of confirmation options
  Serial.println(F("   1. Yes"));
  Serial.println(F("   2. No"));
  Serial.println();

  // Read the selected confirmation option
  do {
    current_selection = Serial.read();
  } while ((current_selection != '1') && (current_selection != '2'));

  // Take the selected action
  switch (current_selection) {
    case '1':
      // Reset the number of sorted M&M's
      resetNumberOfSortedMMs();
      break;
    case '2':
      // Abort the reset process
      Serial.println(F("Reset aborted"));
      Serial.println();
      break;   
  }

  Serial.println(F("Please select an option..."));
  Serial.println();

  // Print the list of navigational options
  Serial.println(F("   1. Return to the sorting data menu"));
  Serial.println(F("   2. Return to the main menu"));
  Serial.println();

  // Read the selected navigational option
  do {
    current_selection = Serial.read();
  } while ((current_selection != '1') && (current_selection != '2'));

  // Print a divider
  printDivider();

  // Call the selected navigational function
  switch (current_selection) {
    case '1':
      printSortingDataMenu();
      break;
    case '2':
      break;   
  }
}

// A function for resetting the number of sorted M&M's stored in the EEPROM
void resetNumberOfSortedMMs() {

  // Reset the number of sorted M&M's stored in the EEPROM
  EEPROM.put(eeAddressTotalNumberOfSortedMMsRed, 0);
  EEPROM.put(eeAddressTotalNumberOfSortedMMsOrange, 0);
  EEPROM.put(eeAddressTotalNumberOfSortedMMsYellow, 0);
  EEPROM.put(eeAddressTotalNumberOfSortedMMsGreen, 0);
  EEPROM.put(eeAddressTotalNumberOfSortedMMsBlue, 0);
  EEPROM.put(eeAddressTotalNumberOfSortedMMsBrown, 0);
  EEPROM.put(eeAddressTotalNumberOfSortedMMsUnknown, 0);

  // Print the completion message
  Serial.println(F("Reset complete"));
  Serial.println();
}

// A function for printing a divider between the different menus
void printDivider() {

  for (int i = 0; i < 72; i++ ) {
    Serial.print(F("-"));
  }

  Serial.println();
  Serial.println();
}

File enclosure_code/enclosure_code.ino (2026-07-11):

// Project name: Smartie Sorter 3000
// Sketch name:  enclosure_code.ino
// Created by:   Pieter van den Berg
// Created on:   28 February 2024

// Code to control the Smartie Sorter 3000's mini arcade game enclosure

#include <EEPROM.h>

// Add the EEPROM addresses for the operating modes
const byte eeAddressChocolateMode = 0;      // enum (1 byte)
const byte eeAddressSortingMode   = 1;      // enum (1 byte)

// Create enums to track the states of the three operating properties
enum SORTING_STATE {
  SORTING,
  NOT_SORTING
};

enum CHOCOLATE_MODE {
  SMARTIES,
  M_AND_M_S
};

enum SORTING_MODE {
  UNCOLLATED,
  COLLATED
};

// Set the default values of the three operating properties
SORTING_STATE sorting_state   = NOT_SORTING;
CHOCOLATE_MODE chocolate_mode = SMARTIES;
SORTING_MODE sorting_mode     = UNCOLLATED;

// Create a bool to keep track of the combinations mode
bool isCombinationsMode = false;

// Create a numeric counter for keeping track of the button presses during combinations mode
int combinationsScore = 0;

// Assign the pin numbers
const int LEDTransistor = 2;
const int button1       = 3;  // The blue arcade game button
const int button2       = 4;  // The left white arcade game button
const int button3       = 5;  // The right white arcade game button

// Create a variable to control the length of the LED flashes
const int LEDFlashingDelay = 200; // [ms]

// Create the variables to keep track of the blue arcade game button's state
int button1Reading       = 0;
int button1StateCurrent  = 0;
int button1StatePrevious = 0;

// Create the variables to keep track of the left white arcade game button's state
int button2Reading       = 0;
int button2StateCurrent  = 0;
int button2StatePrevious = 0;

// Create the variables to keep track of the right white arcade game button's state
int button3Reading       = 0;
int button3StateCurrent  = 0;
int button3StatePrevious = 0;

// Use a debounce delay of 50 ms
unsigned long debounceDelay = 50;  // [ms]

// Create the variables to keep track of the arcade game buttons' last debounce times
unsigned long button1LastDebounceTime = 0;  // [ms]
unsigned long button2LastDebounceTime = 0;  // [ms]
unsigned long button3LastDebounceTime = 0;  // [ms]

void setup() {
  // Setup the transistor pins
  pinMode(LEDTransistor, OUTPUT);

  // Setup the button pins
  pinMode(button1, INPUT);
  pinMode(button2, INPUT);
  pinMode(button3, INPUT);

  // Start the LED lights
  digitalWrite(LEDTransistor, HIGH);

  // Read the operating modes from the EEPROM
  chocolate_mode = (CHOCOLATE_MODE)EEPROM.read(eeAddressChocolateMode);
  sorting_mode   = (SORTING_MODE)EEPROM.read(eeAddressSortingMode);

  // Flash the built-in LEDs 2 times to indicate that the setup is complete
  delay(1000);
  flashLEDs(2);
}

void loop() {
  // Scan for any button presses
  readButtonPresses();

  // Run the sorting procedure when the SORTING_STATE property is set to SORTING
  if (sorting_state == SORTING){


  }
}

// A grouping function for determining whether the arcade game buttons have been pressed
void readButtonPresses(){
  // Determine whether the blue arcade game button has been pressed
  readButton1();
  // Determine whether the left white arcade game button has been pressed
  readButton2();
  // Determine whether the right white arcade game button has been pressed
  readButton3();
}

// A function for determining whether the blue arcade game button has been pressed
void readButton1() {

  // Read the current state of the blue arcade game button
  button1Reading = digitalRead(button1);
 
  // Reset the debounce timer of the blue arcade game button
  if (button1Reading != button1StatePrevious) {
    button1LastDebounceTime = millis();
  }

  // Determine whether the blue arcade game button has been pressed
  if ((millis() - button1LastDebounceTime) > debounceDelay) {
    if (button1Reading != button1StateCurrent) {
      // Update the current state of the blue arcade game button
      button1StateCurrent = button1Reading;
      // Call the button1Pressed() function when the blue arcade game button has been pressed
      if (button1StateCurrent == 1) {
        button1Pressed();
      }
    }
  }

  // Capture the previous state of the blue arcade game button
  button1StatePrevious = button1Reading;
}

// A function for determining whether the left white arcade game button has been pressed
void readButton2() {

  // Read the current state of the left white arcade game button
  button2Reading = digitalRead(button2);
 
  // Reset the debounce timer of the left white arcade game button
  if (button2Reading != button2StatePrevious) {
    button2LastDebounceTime = millis();
  }

  // Determine whether the left white arcade game button has been pressed
  if ((millis() - button2LastDebounceTime) > debounceDelay) {
    if (button2Reading != button2StateCurrent) {
      // Update the current state of the left white arcade game button
      button2StateCurrent = button2Reading;
      // Call the button2Pressed() function when the left white arcade game button has been pressed
      if (button2StateCurrent == 1) {
        button2Pressed();
      }
    }
  }

  // Capture the previous state of the left white arcade game button
  button2StatePrevious = button2Reading;
}

// A function for determining whether the right white arcade game button has been pressed
void readButton3() {

  // Read the current state of the right white arcade game button
  button3Reading = digitalRead(button3);
 
  // Reset the debounce timer of the right white arcade game button
  if (button3Reading != button3StatePrevious) {
    button3LastDebounceTime = millis();
  }

  // Determine whether the right white arcade game button has been pressed
  if ((millis() - button3LastDebounceTime) > debounceDelay) {
    if (button3Reading != button3StateCurrent) {
      // Update the current state of the right white arcade game button
      button3StateCurrent = button3Reading;
      // Call the button3Pressed() function when the right white arcade game button has been pressed
      if (button3StateCurrent == 1) {
        button3Pressed();
      }
    }
  }

  // Capture the previous state of the right white arcade game button
  button3StatePrevious = button3Reading;
}

// Code to run when the blue arcade game button is pressed
void button1Pressed() {

  // Use a switch statement to control the logic for the combinations and normal operating modes
  switch(isCombinationsMode) {
    case false: 
      if (sorting_state == NOT_SORTING) {
        isCombinationsMode = true;
        // Flash the built-in LEDs 3 times to indicate that the Smartie Sorter 3000 has now entered the combinations mode
        flashLEDs(3); 
      }               
      break;
      
    case true:
      isCombinationsMode = false;
      // Evaluate the entered combination
      evaluateCombinations();
      break;
    }   
}
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

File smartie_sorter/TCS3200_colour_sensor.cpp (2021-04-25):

// Library for the TCS3200 colour sensor
// Created by Pieter Leon van den Berg
// on 8 February 2021

#include <Arduino.h>
#include "TCS3200_colour_sensor.h"

// TCS3200_colour_sensor class' contructor
TCS3200_colour_sensor::TCS3200_colour_sensor(int S0, int S1, int S2, int S3, int LED, int OUT)
{
    // Set up the pin values
    _colourSensorS0 = S0;
    _colourSensorS1 = S1;
    _colourSensorS2 = S2;
    _colourSensorS3 = S3;
    _colourSensorLED = LED;
    _colourSensorOut = OUT;   

    // Set up Colour Sensor's pins
    pinMode(_colourSensorS0, OUTPUT);
    pinMode(_colourSensorS1, OUTPUT);
    pinMode(_colourSensorS2, OUTPUT);
    pinMode(_colourSensorS3, OUTPUT);
    pinMode(_colourSensorLED, OUTPUT);
    pinMode(_colourSensorOut, INPUT);
}

// Set up white frequencies for RGB mapping
void TCS3200_colour_sensor::setWhiteFrequencies(int redWhiteFrequency, int greenWhiteFrequency, int blueWhiteFrequency)
{
    _redWhiteFrequency = redWhiteFrequency;
    _greenWhiteFrequency = greenWhiteFrequency;
    _blueWhiteFrequency = blueWhiteFrequency;
}

// Set up black frequencies for RGB mapping
void TCS3200_colour_sensor::setBlackFrequencies(int redBlackFrequency, int greenBlackFrequency, int blueBlackFrequency)
{
    _redBlackFrequency = redBlackFrequency;
    _greenBlackFrequency = greenBlackFrequency;
    _blueBlackFrequency = blueBlackFrequency;
}

// Turn the TCS3200 colour sensor's LEDs on
void TCS3200_colour_sensor::turnOnLEDs()
{
    digitalWrite(_colourSensorLED, HIGH);
}

// Turn the TCS3200 colour sensor's LEDs off
void TCS3200_colour_sensor::turnOffLEDs()
{
    digitalWrite(_colourSensorLED, LOW);
}

// Set scaling frequency of TCS3200 colour sensor to 0%
void TCS3200_colour_sensor::setFrequencyScalingToZero()
{
    digitalWrite(_colourSensorS0, LOW);
    digitalWrite(_colourSensorS1, LOW);
}

// Set scaling frequency of TCS3200 colour sensor to 2%
void TCS3200_colour_sensor::setFrequencyScalingTo2Percent()
{   
    digitalWrite(_colourSensorS0, LOW);
    digitalWrite(_colourSensorS1, HIGH);
}

// Set scaling frequency of TCS3200 colour sensor to 20%
void TCS3200_colour_sensor::setFrequencyScalingTo20Percent()
{
    digitalWrite(_colourSensorS0, HIGH);
    digitalWrite(_colourSensorS1, LOW);   
}

// Set scaling frequency of TCS3200 colour sensor to 100%
void TCS3200_colour_sensor::setFrequencyScalingTo100Percent()
{
    digitalWrite(_colourSensorS0, HIGH);
    digitalWrite(_colourSensorS1, HIGH);     
}

// Read the red frequency returned by the TCS3200 colour sensor
int TCS3200_colour_sensor::readRedFrequency()
{
    int redFrequency;

    // Set up the TCS3200 colour sensor's pins to read the red frequency value
    digitalWrite(_colourSensorS2, LOW);
    digitalWrite(_colourSensorS3, LOW);

    // Read the red colour frequency
    redFrequency = pulseIn(_colourSensorOut, LOW);

    // Return the read frequency
    return redFrequency;
}

// Read the green frequency returned by the TCS3200 colour sensor
int TCS3200_colour_sensor::readGreenFrequency()
{
    int greenFrequency;

    // Set up the TCS3200 colour sensor's pins to read the green frequency value
    digitalWrite(_colourSensorS2, HIGH);
    digitalWrite(_colourSensorS3, HIGH);

    // Read the green colour frequency
    greenFrequency = pulseIn(_colourSensorOut, LOW);

    // Return the read frequency
    return greenFrequency;
}

// Read the blue frequency returned by the TCS3200 colour sensor
int TCS3200_colour_sensor::readBlueFrequency()
{
    int blueFrequency;

    // Set up the TCS3200 colour sensor's pins to read the blue frequency value
    digitalWrite(_colourSensorS2, LOW);
    digitalWrite(_colourSensorS3, HIGH);

    // Read the blue colour frequency
    blueFrequency = pulseIn(_colourSensorOut, LOW);

    // Return the read frequency
    return blueFrequency;
}

// Read the red RGB mapping of the colour read by the TCS3200 colour sensor
int TCS3200_colour_sensor::readRedRGB()
{
    int redRGBValue;
    int redFrequency;

    // Read the red frequency returned by the TCS3200 colour sensor
    redFrequency = readRedFrequency();

    // Map the frequency to the corresponding RGB value
    redRGBValue = map(redFrequency, _redWhiteFrequency, _redBlackFrequency, 255, 0);

    // Limit the upper value
    if (redRGBValue > 255)
    {
    redRGBValue = 255;
    }

    // Limit the lower value
    if (redRGBValue < 0)
    {
    redRGBValue = 0;
    }

    // Return the mapped red RGB value
    return redRGBValue;
}

// Read the green RGB mapping of the colour read by the TCS3200 colour sensor
int TCS3200_colour_sensor::readGreenRGB()
{
    int greenRGBValue;
    int greenFrequency;

    // Read the green frequency returned by the TCS3200 colour sensor
    greenFrequency = readGreenFrequency();

    // Map the frequency to the corresponding RGB value
    greenRGBValue = map(greenFrequency, _greenWhiteFrequency, _greenBlackFrequency, 255, 0);

    // Limit the upper value
    if (greenRGBValue > 255)
    {
    greenRGBValue = 255;
    }

    // Limit the lower value
    if (greenRGBValue < 0)
    {
    greenRGBValue = 0;
    }

    // Return the mapped green RGB value
    return greenRGBValue;
}

// Read the blue RGB mapping of the colour read by the TCS3200 colour sensor
int TCS3200_colour_sensor::readBlueRGB()
{
    int blueRGBValue;
    int blueFrequency;

    // Read the blue frequency returned by the TCS3200 colour sensor
    blueFrequency = readBlueFrequency();

    // Map the frequency to the corresponding RGB value
    blueRGBValue = map(blueFrequency, _blueWhiteFrequency, _blueBlackFrequency, 255, 0);

    // Limit the upper value
    if (blueRGBValue > 255)
    {
    blueRGBValue = 255;
    }

    // Limit the lower value
    if (blueRGBValue < 0)
    {
    blueRGBValue = 0;
    }

    // Return the mapped blue RGB value
    return blueRGBValue;
}

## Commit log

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2021-01-08 Fixed to call the correct RGB mapping
    [smartie_sorter.ino]
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2021-01-09 Prompt for colour of Smartie to calibrate
    Created a prompt to place the correct coloured Smartie in front of the colour sensor to start calibration for that colour Smartie
    [smartie_sorter.ino]
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2021-01-11 Corrected spelling of "unknown" Smartie
    [smartie_sorter.ino]
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2021-02-24 Corrected to open image of colour sensor enclosure
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2024-02-24 Added proposed smartie colour detection mechanism .f3z file
    [proposed_smartie_colour_detection_mechanism.f3z]
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2025-04-10 Added the Unsorted Smarties Holder Finger Joints panels
    [back_panel.f3d, bottom_panel.f3d, front_panel.f3d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]
2025-04-10 Added the Sorted Smarties Collector Finger Joints panels
    [back_panel.f3d, divider_bottom.f3d, divider_top.f3d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]
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2025-04-11 Added the Unsorted Smarties Holder Finger Joints dxf files
    [back_panel.dxf, bottom_panel.dxf, front_panel.dxf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]
2025-04-11 Added the Sorted Smarties Collector Finger Joints dxf files
    [back_panel.dxf, divider_bottom.dxf, divider_top.dxf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]
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2025-05-01 Added a hole for the Colour Detection Mechanism's wires
    [sorting_mechanism_conduit.f3d]
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2025-05-14 Renamed Sorting Mechanism Top Panel to Colour Detection Mechanism Top Panel
    [colour_detection_mechanism_top_panel.dxf, colour_detection_mechanism_top_panel.f3d]
2025-05-14 Added the Colour Detection Mechanism Top Panel Supports
    [colour_detection_mechanism_top_panel_support.f3d]
2025-05-19 Added the Colour Detection Mechanism Top Panel to the Smartie Sorter 3000
    [colour_detection_mechanism_top_panel_placeholder.f3d]
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2025-05-19 Added the Sorted Smarties Collector Finger Joints to the Smartie Sorter 3000
    [sorted_smarties_collector.f3d, sorted_smarties_collector_finger_joints.f3d]
2025-05-19 Renamed the "Sorted Smarties Collector Finger Joints" to "Sorted Smarties Collector"
    [back_panel.f3d, divider_bottom.f3d, divider_top.f3d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]
2025-05-19 Changed the appearances of the individual Sorted Smarties Collector acrylic panels
    [back_panel.f3d, divider_bottom.f3d, divider_top.f3d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]
2025-05-20 Linked the Unsorted Smarties Holder Finger Joints Assembly to the individual panels
    [unsorted_smarties_holder_finger_joints.f3d, unsorted_smarties_holder_finger_joints.f3z]
2025-05-20 Added the Smartie slide to the Unsorted Smarties Holder Finger Joints assembly and updated the appearance of the Unsorted Smarties Holder Finger Joints panels to clear acrylic
    [back_panel.f3d, bottom_panel.f3d, front_panel.f3d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]
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2025-05-20 Renamed the Unsorted Smarties Holder Finger Joints to Smartie Slide
    [back_panel.f3d, bottom_panel.f3d, front_panel.f3d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]
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2025-05-24 Renamed the Sorting Mechanism Platform to Colour Detection Mechanism Platform
    [colour_detection_mechanism_platform.f3d]
2025-05-24 Renamed the Servo Motor Top to Servo Horn
    [servo_horn.f3d]
2025-05-24 Updated the Colour Detection Mechanism Platform and the Smartie Arm
    [colour_detection_mechanism_platform.f3d, smartie_arm.f3d]
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2025-05-24 Added the Colour Detection Mechanism assembly to the Smartie Sorter 3000 assembly
    [colour_detection_mechanism.f3z]
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2025-06-11 Changed the Colour Detection Mechanism Top Panel's width to 270 mm
    [colour_detection_mechanism_top_panel.f3d]
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2025-07-08 Added tolerances to the back panel
    [back_panel.dxf, back_panel.f3d, smartie_sorter_3000.f3z]
2025-07-08 Added tolerances to the top access panel
    [smartie_sorter_3000.f3z, top_access_panel.dxf, top_access_panel.f3d]
2025-07-08 Added tolerances to the bottom access panel
    [bottom_access_panel.dxf, bottom_access_panel.f3d, smartie_sorter_3000.f3z]
2025-07-09 Updated the positions of the Top Access Panel and Bottom Access Panel labels
    [smartie_sorter_3000.f3z]
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2025-07-16 Added functions that ask for confirmation before resetting the number of sorted Smarties and M&M's
    [calibration.ino]
2025-07-16 Added a function for resetting the number of sorted Smarties
    [calibration.ino]
2025-07-16 Added a function for resetting the number of sorted M&M's
    [calibration.ino]
2025-07-21 Added a description of what initialising the EEPROM will reset
    [calibration.ino]
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2025-07-26 Updated the batteries to use the Energizer Ultimate Lithium colour scheme
    [3V_battery_compartment.f3d, 9V_battery_compartment.f3d, smartie_sorter_3000.f3z]
2025-07-28 Added the laser-cutting tolerances to the Smartie Slide's Back Panel
    [back_panel.dxf, back_panel.f3d]
2025-07-28 Added the laser-cutting tolerances to the Smartie Slide's Top Panel
    [top_panel.dxf, top_panel.f3d]
2025-07-28 Added the laser-cutting tolerances to the Smartie Slide's Middle Panel
    [middle_panel.dxf, middle_panel.f3d]
2025-07-28 Added the laser-cutting tolerances to the Smartie Slide's Front Panel
    [front_panel.dxf, front_panel.f3d]
2025-07-28 Added the laser-cutting tolerances to the Smartie Slide assembly
    [smartie_slide.f3z, smartie_sorter_3000.f3z]
2025-07-28 Added the laser-cutting tolerances to the Sorted Smarties Collector's Back Panel
    [back_panel.dxf, back_panel.f3d]
2025-07-28 Added the laser-cutting tolerances to the Sorted Smarties Collector's Horizontal Panel
    [horizontal_panel.dxf, horizontal_panel.f3d]
2025-07-28 Added the laser-cutting tolerances to the Sorted Smarties Collector's Side Panel
    [side_panel.dxf, side_panel.f3d]
2025-07-28 Added the laser-cutting tolerances to the Sorted Smarties Collector's Top Panel
    [top_panel.dxf, top_panel.f3d]
2025-07-28 Added the laser-cutting tolerances to the Sorted Smarties Collector assembly
    [smartie_sorter_3000.f3z, sorted_smarties_collector.f3z]
2025-07-29 Added the LED strips to the DXF files of the Unsorted Smarties Top Panel and the Sorted Smarties Top Panel
    [sorted_smarties_top_panel.dxf, unsorted_smarties_top_panel.dxf]
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2025-08-24 Updated the Colour Detection Mechanism Top Panel Support
    [colour_detection_mechanism_top_panel_support.f3d, smartie_sorter_3000.f3z]
2025-08-24 Updated the heights of the pins on the back of the TCS3200 colour sensor
    [TCS3200_colour_sensor.f3d]
2025-08-26 Created the Colour Sensor Holder and Cover Sensor Cover
    [colour_sensor_cover.f3d, colour_sensor_holder.f3d]
2025-08-27 Added the Colour Sensor Holder hole to the Colour Detection Mechanism Platform
    [colour_detection_mechanism.f3z, colour_detection_mechanism_platform.f3d]
2025-08-28 Added the Colour Detection Mechanism Conduit's shape to the Colour Sensor Holder
    [colour_sensor_holder.f3d]
2025-08-28 Added the Colour Detection Mechanism Conduit chamfer to the Colour Sensor Holder
    [colour_sensor_holder.f3d]
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2025-09-07 Removed the Colour Sensor Servo Seat from the Colour Detection Mechanism Platform
    [colour_detection_mechanism_platform.f3d]
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2025-09-27 Added the Colour Sensor Servo Seat and the updated Savöx SH 0255 MG Micro Servo components to the Colour Detection Mechanism assembly
    [colour_detection_mechanism.f3z]
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2025-12-26 Added the 5 Volt, 6 Volt, and 12 Volt labels to the Smartie Sorter assembly
    [smartie_sorter_3000.f3z]
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2026-01-11 Updated the diameter of the hole of the Smartie Arm to 15.5 mm
    [smartie_arm.f3d]
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2026-01-20 Added a 10 degree angle to the front side of the Smartie Hopper
    [smartie_hopper.f3d]
2026-01-21 Added offset parameters to ensure that the bottom outlet hole of the Smartie Hopper is directly above the hole of the Smartie Arm
    [smartie_hopper.f3d]
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
